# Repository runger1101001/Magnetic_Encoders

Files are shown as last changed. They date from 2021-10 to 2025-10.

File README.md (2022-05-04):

# Small encoder boards

Several designs for small magnetic encoder boards.
These boards all serve the same purpose, and many have the same shapes. They use different sensor ICs, which depending on the IC may result in different performance or different interface types.

They are intended to sense the absolute angular position of a rotating magnet. Generally this is used to sense the position of a motor shaft, as an input to motor control algorithms, or a joint/actuator position, for robotics applcations.

Where sensors use I2C, they use the Stemma-QT/Qwiic connectors (JST-SH) and pinouts.
Where sensors use SPI or SSI, they all use the same pinouts.

:warning: Not all of these have been produced or tested.

Please consult the individual subdirectories for more information. If a sub-directory does not contain a README, use at your own risk.

## Finished and tested designs

- [AS5048A](./Encoder_SPI/)
- [AS5048B](./Encoder/)
- [TLE5012B](./Encoder_SPI_TLE5012B/)
- [SC60228](./Encoder_SPI_SC60228/)

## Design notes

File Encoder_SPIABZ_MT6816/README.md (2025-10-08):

# MT6816 magnetic angle sensor

Small (21x17mm) board for the MT6816 magnetic absolute angle sensor.

For use in motor control or robotics applications, the sensor measures the orientation (angle in the plane) of a nearby diametrically magnetized magnet.

That sounds more complicated than using it really is, so lets describe it another way:

- attach the magnet to the axis of something that rotates
- put the sensor near it
- read angles with your Arduino

| Back of board | Front of board |
| --- | --- |
| with SH 1.0 connectors <br> | with sensor <br> |

## Features

- 3V to 5.5V operation
- 14 bit accuracy, 16384 positions per revolution
- SPI interface up to 15MHz
- PWM output pin with 1kHz PWM frequency and 12bit accuracy
- ABZ interface with 12 bit accuracy, 4096 steps in quadrature mode
- power indication LED (green, dim)

Datasheet of the sensor: https://www.novosns.com/enfiles/MT6816_Rev.2.1.pdf

## Getting one

You may be able to buy some here:



Or you could make one - it is open source, you will find gerber files and BOM in the repo, and design files for KiCad 6.

## Usage

The sensor has to be precisely positioned near the magnet. The magnet should be precisely on-axis and in-plane (no wobble!). The sensor should be mounted with an air-gap of about 0.5mm to the magnet.

Taking the time to mount the magnet and sensor board carefully will improve the accuracy and smoothness of your readings.

The sensor has SPI and ABZ interfaces, selectable by switch:

| SPI | ABZ |
| --- | --- |
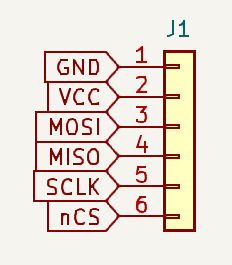
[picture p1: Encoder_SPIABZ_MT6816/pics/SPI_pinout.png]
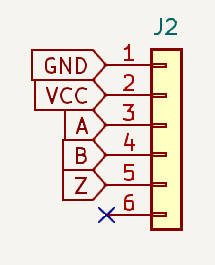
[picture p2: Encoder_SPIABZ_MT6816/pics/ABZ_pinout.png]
|  |  |

The SPI and ABZ interfaces are output on a JST-SH 6-pin socket. Pre-made cables are available cheaply on AliExpress and other sources.

You may connect VCC to either 3.3V or 5V.

For SPI, connect the other lines (MOSI, MISO, CLK and CS) to the respective counterparts on your MCU board.
Note: The sensor board does not pull the CS line up.

The ABZ and SPI outputs cannot be used at the same time. Use the switch to select the output mode.

## Communications

SPI interface:

- SPI Mode 3
- MSB first
- max 15MHz SPI clock

See [datasheet](https://www.novosns.com/enfiles/MT6816_Rev.2.1.pdf) for details, or use an existing software driver.

:warning: Note: cable length, shielding (or lack thereof) and environmental noise may limit performance to significantly less than the 10MHz maximum.

## Software

The sensor can be used with any appropriate SPI driver.

The author uses it with Arduino-compatible MCU boards and the [SimpleFOC library](http://www.simplefoc.com).

A driver for the sensor for Arduino and SimpleFOC can be found here: [SimpleFOC drivers library](https://github.com/simplefoc/Arduino-FOC-drivers/tree/master/src/encoders/mt6816)

## Physical dimensions

v1.0: 21 x 17 x 4mm (1.6mm PCB)

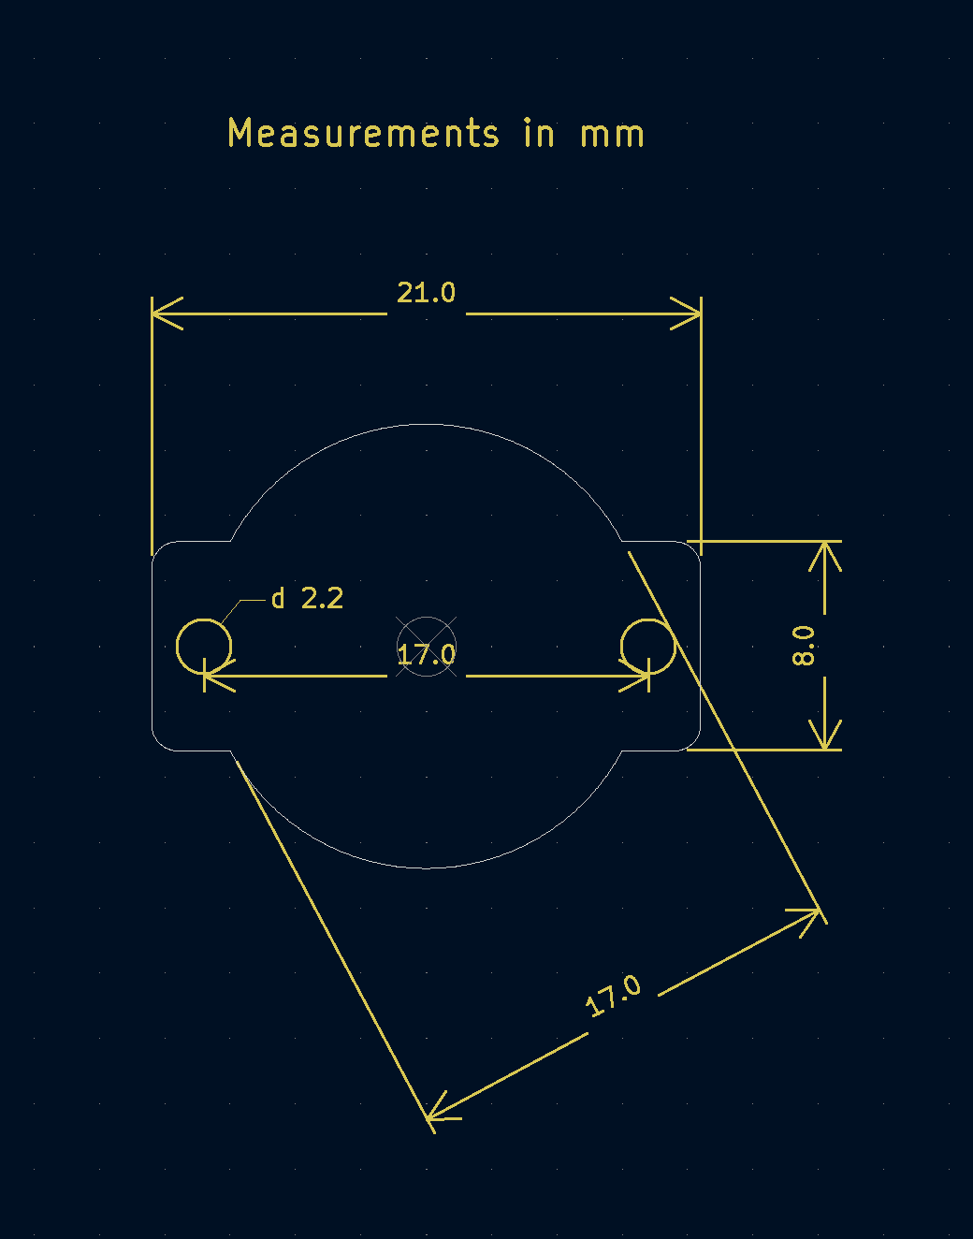
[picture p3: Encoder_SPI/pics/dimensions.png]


## Cables

Pre-made JST SH 1.0 cables are available. When buying cables with two plugs, choose the type that is called "reverse connection" - where the pins on both ends of the cable have the same order.

Some links to compatible cables / breakout boards:

- https://www.tindie.com/products/26431/
- https://www.aliexpress.com/item/4000421829259.html
- https://www.aliexpress.com/item/4001235017139.html
- https://www.pololu.com/product/4770
- https://www.pololu.com/product/4772

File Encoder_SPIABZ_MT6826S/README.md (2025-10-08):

# MT6826S magnetic angle sensor

Small (21x17mm) board for the MT6826S magnetic absolute angle sensor.

For use in motor control or robotics applications, the sensor measures the orientation (angle in the plane) of a nearby diametrically magnetized magnet.

That sounds more complicated than using it really is, so lets describe it another way:
- attach the magnet to the axis of something that rotates
- put the sensor near it
- read angles with your Arduino

| Back of board | Front of board |
| --- | --- |
| with SH 1.0 connectors <br> | with sensor <br> |

## Features

- 3V to 5V operation
- 15 bit accuracy, 32768 positions per revolution 
- SPI interface up to 15Hz
- PWM output pin with 1kHz PWM frequency and 12bit accuracy
- ABZ interface with 14 bit accuracy, 16384 steps in quadrature mode
- power indication LED (green, dim)

Datasheet of the sensor: https://www.novosns.com/enfiles/MT6826S_Datasheet_Rev.1.1.pdf

## Getting one

You may be able to buy some here:



Or you could make one - it is open source, you will find gerber files and BOM in the repo, and design files for KiCad 6.

## Usage

The sensor has to be precisely positioned near the magnet. The magnet should be precisely on-axis and in-plane (no wobble!). The sensor should be mounted with an air-gap of about 0.5mm to the magnet.

Taking the time to mount the magnet and sensor board carefully will improve the accuracy and smoothness of your readings.

The sensor has SPI and ABZ interfaces:

|SPI|ABZ|
|---|---|
|||

The SPI interface is available on a JST-SH 6-pin socket. Pre-made cables are available cheaply on AliExpress and other sources.

You may connect VCC to either 3.3V or 5V, but must set the solder jumper accordingly. The default setting of the solder jumper is 3.3V. To use 5V power, carefully cut the trace connecting the two pads of the jumper. 

For SPI, connect the other lines (MOSI, MISO, CLK and CS) to the respective counterparts on your MCU board.

The ABZ outputs can be used in parallel to the SPI interface.

Note: The sensor board does not pull the CS line up.

## Communications

SPI interface:
- SPI Mode 3
- MSB first
- max 15MHz SPI clock

See [datasheet](https://www.novosns.com/enfiles/MT6826S_Datasheet_Rev.1.1.pdf) for details, or use an existing software driver.

:warning: Note: cable length, shielding (or lack thereof) and environmental noise may limit performance to significantly less than the 10MHz maximum.

## Software

The sensor can be used with any appropriate SPI driver.

The author uses it with Arduino-compatible MCU boards and the [SimpleFOC library](http://www.simplefoc.com).

A driver for the sensor for Arduino and SimpleFOC can be found here: [SimpleFOC drivers library](https://github.com/simplefoc/Arduino-FOC-drivers/tree/master/src/encoders/mt6826s)

## Physical dimensions

v1.0: 21 x 17 x 4mm (1.6mm PCB)



## Cables

Pre-made JST SH 1.0 cables are available. When buying cables with two plugs, choose the type that is called "reverse connection" - where the pins on both ends of the cable have the same order.

Some links to compatible cables / breakout boards:

 - https://www.tindie.com/products/26431/
 - https://www.aliexpress.com/item/4000421829259.html
 - https://www.aliexpress.com/item/4001235017139.html
 - https://www.pololu.com/product/4770
 - https://www.pololu.com/product/4772

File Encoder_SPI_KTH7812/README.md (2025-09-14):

# KTH7812 magnetic angle sensor

Small (21x17mm) board for the KTH7812 magnetic absolute angle sensor with high resolution.

For use in motor control or robotics applications, the sensor measures the orientation (angle in the plane) of a nearby diametrically magnetized magnet.

That sounds more complicated than using it really is, so lets describe it another way:
- attach the magnet to the axis of something that rotates
- put the sensor near it
- read angles with your Arduino

| Back of board | Front of board |
| --- | --- |
| with SH 1.0 connector  | with sensor  |

## Features

- 3.3V to 5V operation
- 16 bit resolution, 65536 positions per revolution
- SPI interface up to 10MHz
- power indication LED (green, dim)

Datasheet of the sensor: [KTH7812_产品手册.pdf](https://en.conntek.com.cn/html/web/product/magneticAngleDetectionChip/hshrMagneticCodedAngleSensor/index.html
https://en.conntek.com.cn/api/resource/freeDownload?name=KTH7812%20产品手册.pdf)

## Getting one

You may be able to buy some here:



Or you could make one - it is open source, you will find gerber files and BOM in the repo, and design files for KiCad 9.

## Usage

The sensor has to be precisely positioned near the magnet. The magnet should be precisely on-axis and in-plane (no wobble!). The sensor should be mounted with an air-gap of about 0.5mm to the magnet.

Taking the time to mount the magnet and sensor board carefully will improve the accuracy and smoothness of your readings.

The sensor has an SPI interface:

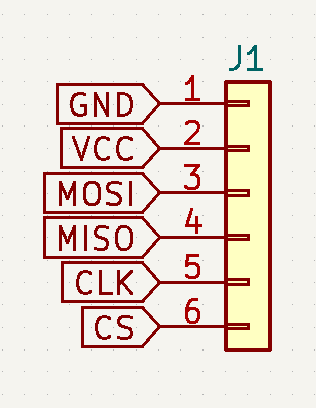
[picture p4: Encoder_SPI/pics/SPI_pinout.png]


The SPI interface is available on a JST-SH 6-pin socket. Pre-made cables are available cheaply on AliExpress and other sources.

You may connect VCC to either 3.3V or 5V. 

Connect the other lines (MOSI, MISO, CLK and CS) to the respective counterparts on your MCU board.

Note: The sensor board does not pull the CS line up.

## Communications

SPI interface:
- SPI Mode 3
- MSB first
- max 10MHz SPI clock

See [datasheet](https://en.conntek.com.cn/html/web/product/magneticAngleDetectionChip/hshrMagneticCodedAngleSensor/index.html
https://en.conntek.com.cn/api/resource/freeDownload?name=KTH7812%20产品手册.pdf) for details, or use an existing software driver.

:warning: Note: cable length, shielding (or lack thereof) and environmental noise may limit performance to significantly less than the 10MHz maximum.

## Software

The sensor can be used with any appropriate SPI driver.

The author uses it with Arduino-compatible MCU boards and the [SimpleFOC library](http://www.simplefoc.com).

A driver for the sensor for Arduino and SimpleFOC can be found here: [SimpleFOC drivers library](https://github.com/simplefoc/Arduino-FOC-drivers/tree/master/src/encoders/KTH7812)

## Physical dimensions

v1.0: 21 x 17 x 4mm (1.6mm PCB)



## Cables

Pre-made JST SH 1.0 cables are available. When buying cables with two plugs, choose the type that is called "reverse connection" - where the pins on both ends of the cable have the same order.

Some links to compatible cables / breakout boards:

 - https://www.tindie.com/products/26431/
 - https://www.aliexpress.com/item/4000421829259.html
 - https://www.aliexpress.com/item/4001235017139.html
 - https://www.pololu.com/product/4770
 - https://www.pololu.com/product/4772

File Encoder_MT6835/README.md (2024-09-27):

# MT6835 magnetic angle sensor

Small (21x17mm) board for the MT6835 magnetic absolute angle sensor.

For use in motor control or robotics applications, the sensor measures the orientation (angle in the plane) of a nearby diametrically magnetized magnet.

That sounds more complicated than using it really is, so lets describe it another way:
- attach the magnet to the axis of something that rotates
- put the sensor near it
- read angles with your Arduino

| Back of board | Front of board |
| --- | --- |
| with SH 1.0 connectors <br> | with sensor <br> |

## Features

- 3V to 5V operation
- 21 bit accuracy, 2097152 positions per revolution (!)
- ABZ interface with 16 bit accuracy, 65536 steps in quadrature mode (!)
- SPI interface up to 15MHz
- PWM output pin with 994Hz PWM frequency and 12bit accuracy
- On-chip linearity calibration
- power indication LED (green, dim)

Datasheet of the sensor: https://www.magntek.com.cn/upload/MT6835_Rev.1.3.pdf

## Getting one

You may be able to buy some here:



Or you could make one - it is open source, you will find gerber files and BOM in the repo, and design files for KiCad 6.

## Usage

The sensor has to be precisely positioned near the magnet. The magnet should be precisely on-axis and in-plane (no wobble!). The sensor should be mounted with an air-gap of about 0.5mm to the magnet.

Taking the time to mount the magnet and sensor board carefully will improve the accuracy and smoothness of your readings.

The sensor has SPI and ABZ interfaces:

|SPI|ABZ|
|---|---|
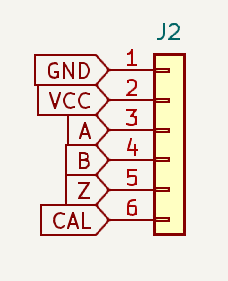
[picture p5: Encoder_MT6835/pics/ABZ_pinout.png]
|||

The SPI interface is available on a JST-SH 6-pin socket. Pre-made cables are available cheaply on AliExpress and other sources.

You may connect VCC to either 3.3V or 5V.

For SPI, connect the other lines (MOSI, MISO, CLK and CS) to the respective counterparts on your MCU board.

The ABZ outputs can be used in parallel to the SPI interface.

The CAL pin on the ABZ interface gives feedback on the built-in calibration procedure (see datasheet). It can be ignored if not needed.

Note: the sensor chip's ABZ interface is disabled by default. You have to enable it and set the resolution using the SPI interface.

Note: The sensor board does not pull the CS line up.

## Communications

SPI interface:
- SPI Mode 3
- MSB first
- max 15MHz SPI clock

See [datasheet](https://www.magntek.com.cn/upload/MT6835_Rev.1.3.pdf) for details, or use an existing software driver.

:warning: Note: cable length, shielding (or lack thereof) and environmental noise may limit performance to significantly less than the 15MHz maximum.

## Software

The sensor can be used with any appropriate SPI driver.

The author uses it with Arduino-compatible MCU boards and the [SimpleFOC library](http://www.simplefoc.com).

A driver for the sensor for Arduino and SimpleFOC can be found here: [SimpleFOC drivers library](https://github.com/simplefoc/Arduino-FOC-drivers/tree/master/src/encoders/mt6835)

## Physical dimensions

v1.0: 21 x 17 x 4mm (1.6mm PCB)



3D model: [STEP file](./Encoder_MT6835.step)

## Cables

Pre-made JST SH 1.0 cables are available. When buying cables with two plugs, choose the type that is called "reverse connection" - where the pins on both ends of the cable have the same order.

Some links to compatible cables / breakout boards:

 - https://www.tindie.com/products/26431/
 - https://www.aliexpress.com/item/4000421829259.html
 - https://www.aliexpress.com/item/4001235017139.html
 - https://www.pololu.com/product/4770
 - https://www.pololu.com/product/4772

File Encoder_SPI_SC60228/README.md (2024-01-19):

# SC60228 magnetic angle sensor

Small (21x17mm) board for the SC60228 magnetic absolute angle sensor.

For use in motor control or robotics applications, the sensor measures the orientation (angle in the plane) of a nearby diametrically magnetized magnet.

That sounds more complicated than using it really is, so lets describe it another way:
- attach the magnet to the axis of something that rotates
- put the sensor near it
- read angles with your Arduino

| Back of board | Front of board |
| --- | --- |
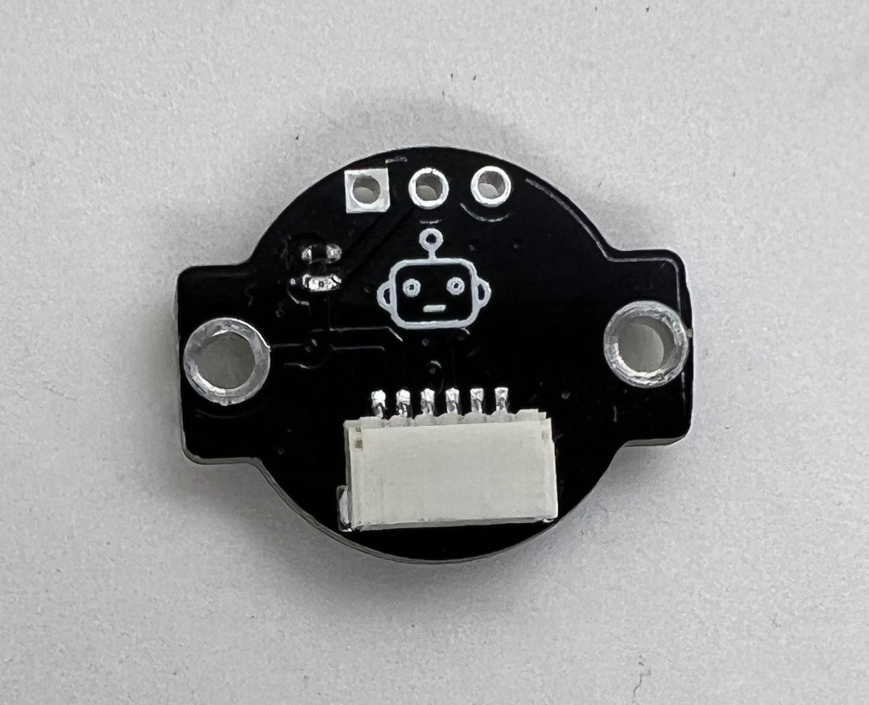
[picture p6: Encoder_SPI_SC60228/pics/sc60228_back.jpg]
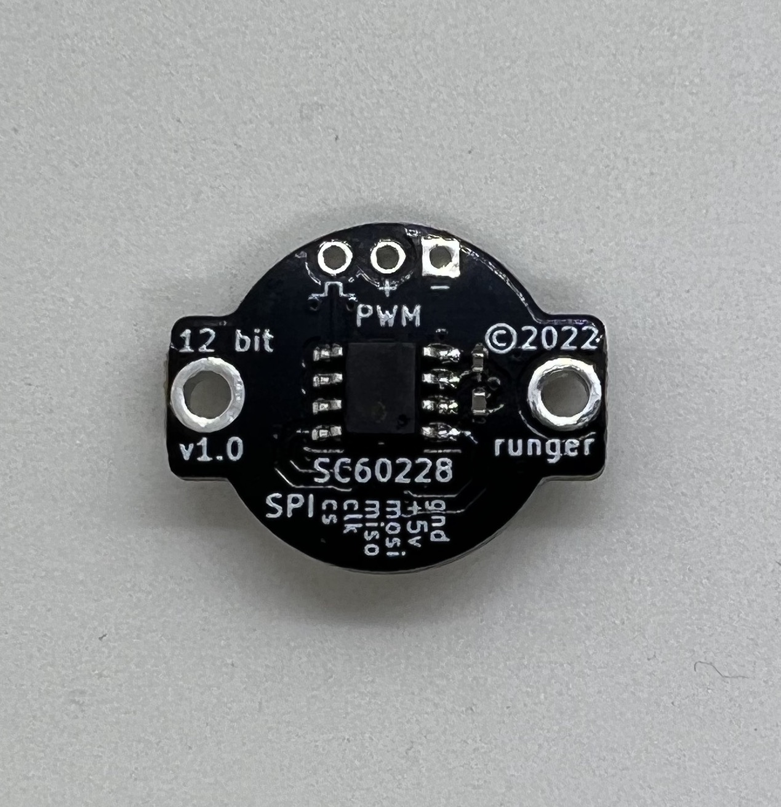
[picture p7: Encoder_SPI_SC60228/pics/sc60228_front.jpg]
| with SH 1.0 connector  | with sensor  |

## Features

- 3V to 5V operation
- 12 bit accuracy, 4096 positions per revolution 
- SPI interface up to 10MHz
- power indication LED (green, dim)

Datasheet of the sensor: http://www.semiment.com/download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

## Getting one

You may be able to buy some here:



Or you could make one - it is open source, you will find gerber files and BOM in the repo, and design files for KiCad 6.

## Usage

The sensor has to be precisely positioned near the magnet. The magnet should be precisely on-axis and in-plane (no wobble!). The sensor should be mounted with an air-gap of about 0.5mm to the magnet.

Taking the time to mount the magnet and sensor board carefully will improve the accuracy and smoothness of your readings.

The sensor has an SPI interface:



The SPI interface is available on a JST-SH 6-pin socket. Pre-made cables are available cheaply on AliExpress and other sources.

You may connect VCC to either 3.3V or 5V. 

Connect the other lines (MOSI, MISO, CLK and CS) to the respective counterparts on your MCU board.

Note: The sensor board does not pull the CS line up.

## Communications

SPI interface:
- SPI Mode 1
- MSB first
- max 10MHz SPI clock

See [datasheet](http://www.semiment.com/download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) for details, or use an existing software driver.

:warning: Note: cable length, shielding (or lack thereof) and environmental noise may limit performance to significantly less than the 10MHz maximum.

## Software

The sensor can be used with any appropriate SPI driver.

The author uses it with Arduino-compatible MCU boards and the [SimpleFOC library](http://www.simplefoc.com).

A driver for the sensor for Arduino and SimpleFOC can be found here: [SimpleFOC drivers library](https://github.com/simplefoc/Arduino-FOC-drivers/tree/master/src/encoders/sc60228)

## Physical dimensions

v1.0: 21 x 17 x 4mm (1.6mm PCB)



## Cables

Pre-made JST SH 1.0 cables are available. When buying cables with two plugs, choose the type that is called "reverse connection" - where the pins on both ends of the cable have the same order.

Some links to compatible cables / breakout boards:

 - https://www.tindie.com/products/26431/
 - https://www.aliexpress.com/item/4000421829259.html
 - https://www.aliexpress.com/item/4001235017139.html
 - https://www.pololu.com/product/4770
 - https://www.pololu.com/product/4772

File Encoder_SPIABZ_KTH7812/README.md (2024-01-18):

# AS5047P magnetic angle sensor

Small (21x17mm) board for the AS5047P magnetic absolute angle sensor.

For use in motor control or robotics applications, the sensor measures the orientation (angle in the plane) of a nearby diametrically magnetized magnet.

That sounds more complicated than using it really is, so lets describe it another way:
- attach the magnet to the axis of something that rotates
- put the sensor near it
- read angles with your Arduino

| Back of board | Front of board |
| --- | --- |
| with SH 1.0 connectors <br> | with sensor <br> |

## Features

- 3V to 5V operation
- 14 bit accuracy, 16384 positions per revolution 
- SPI interface up to 10MHz
- PWM output pin with 1kHz PWM frequency and 12bit accuracy
- ABZ interface with 12 bit accuracy, 4096 steps in quadrature mode
- power indication LED (green, dim)

Datasheet of the sensor: https://ams.com/documents/20143/36005/AS5047P_DS000324_3-00.pdf

## Getting one

You may be able to buy some here:



Or you could make one - it is open source, you will find gerber files and BOM in the repo, and design files for KiCad 6.

## Usage

The sensor has to be precisely positioned near the magnet. The magnet should be precisely on-axis and in-plane (no wobble!). The sensor should be mounted with an air-gap of about 0.5mm to the magnet.

Taking the time to mount the magnet and sensor board carefully will improve the accuracy and smoothness of your readings.

The sensor has SPI and ABZ interfaces:

|SPI|ABZ|
|---|---|
|||

The SPI interface is available on a JST-SH 6-pin socket. Pre-made cables are available cheaply on AliExpress and other sources.

You may connect VCC to either 3.3V or 5V, but must set the solder jumper accordingly. The default setting of the solder jumper is 3.3V. To use 5V power, carefully cut the trace connecting the two pads of the jumper. 

For SPI, connect the other lines (MOSI, MISO, CLK and CS) to the respective counterparts on your MCU board.

The ABZ outputs can be used in parallel to the SPI interface.

Note: The sensor board does not pull the CS line up.

## Communications

SPI interface:
- SPI Mode 1
- MSB first
- max 10MHz SPI clock

See [datasheet](https://ams.com/documents/20143/36005/AS5047P_DS000324_3-00.pdf) for details, or use an existing software driver.

:warning: Note: cable length, shielding (or lack thereof) and environmental noise may limit performance to significantly less than the 10MHz maximum.

## Software

The sensor can be used with any appropriate SPI driver.

The author uses it with Arduino-compatible MCU boards and the [SimpleFOC library](http://www.simplefoc.com).

A driver for the sensor for Arduino and SimpleFOC can be found here: [SimpleFOC drivers library](https://github.com/simplefoc/Arduino-FOC-drivers/tree/master/src/encoders/as5047)

## Physical dimensions

v1.0: 21 x 17 x 4mm (1.6mm PCB)



3D model: [STEP file](./Encoder_SPI_AS5047P.step)

## Cables

Pre-made JST SH 1.0 cables are available. When buying cables with two plugs, choose the type that is called "reverse connection" - where the pins on both ends of the cable have the same order.

Some links to compatible cables / breakout boards:

 - https://www.tindie.com/products/26431/
 - https://www.aliexpress.com/item/4000421829259.html
 - https://www.aliexpress.com/item/4001235017139.html
 - https://www.pololu.com/product/4770
 - https://www.pololu.com/product/4772

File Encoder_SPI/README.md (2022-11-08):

# AS5048A magnetic angle sensor

Small (21x17mm) board for the AS5048A magnetic absolute angle sensor.

For use in motor control or robotics applications, the sensor precisely measures the orientation (angle in the plane) of a nearby diametrically magnetized magnet.

That sounds more complicated than using it really is, so lets describe it another way:
- attach the magnet to the axis of something that rotates
- put the sensor near it
- read precise angles with your Arduino

| Back of board | Front of board |
| --- | --- |
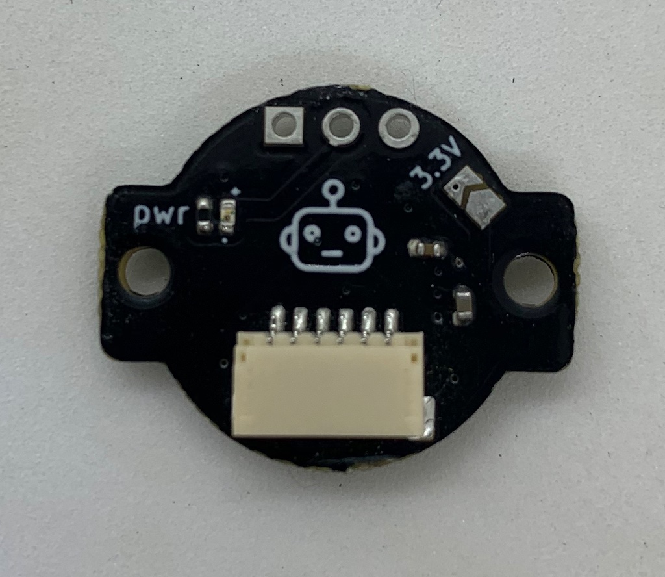
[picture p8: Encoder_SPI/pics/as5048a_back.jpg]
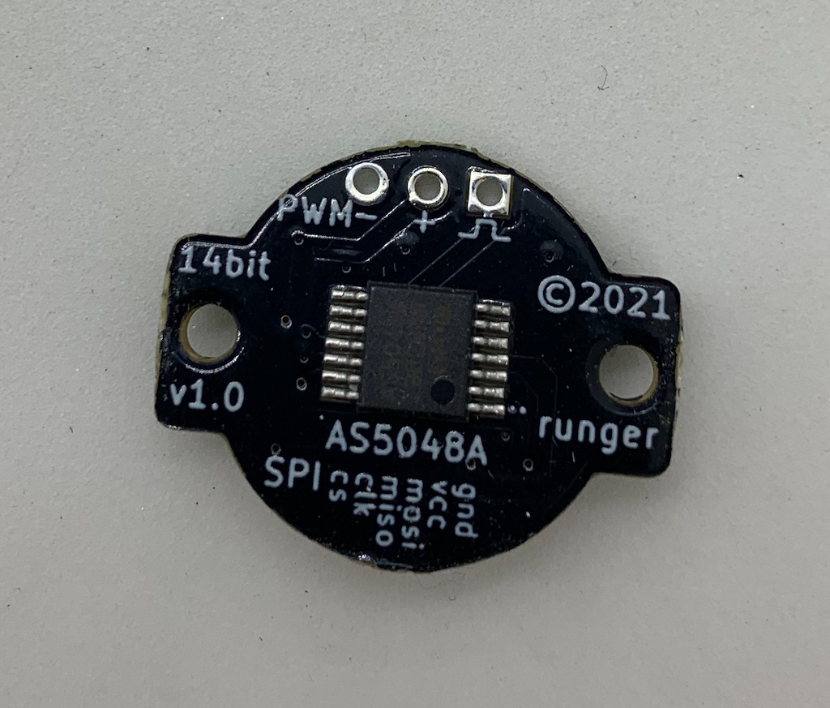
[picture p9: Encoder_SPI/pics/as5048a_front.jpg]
| with SH 1.0 connector  | with sensor  |

## Features

- 3.3V (default) or 5V (break solder bridge for 5V)
- 14 bit accuracy, 16384 positions per revolution 
- SPI interface up to 10MHz
- PWM output pin with 1kHz PWM frequency and 12bit accuracy
- power indication LED (green, dim)

Datasheet of the sensor: https://ams.com/documents/20143/36005/AS5048_DS000298_4-00.pdf

## Getting one

You may be able to buy some here:



Or you could make one - it is open source, you will find gerber files and BOM in the repo, and design files for KiCad 6.

## Getting help

Please visit our discord: https://discord.gg/FwTymtVhMU

Or if you have found a problem, you can also open a bug-ticket here on GitHub.

## Usage

The sensor has to be precisely positioned near the magnet. The magnet should be precisely on-axis and in-plane (no wobble!). The sensor should be mounted with an air-gap of about 0.5mm to the magnet.

Taking the time to mount the magnet and sensor board carefully will improve the accuracy and smoothness of your readings.

The sensor has an SPI interface:



The SPI interface is available on a JST-SH 6-pin socket. Pre-made cables are available cheaply on AliExpress and other sources.

You may connect VCC to either 3.3V or 5V. 

Sensor board v1.1 (current version):

- If using 5V, break the connection between the solder bridge pads on the back side of the board.
- If using 3.3V, leave as is, do not break the solder-bridge.

Sensor board v1.0 (older version):

- If using 5V, leave the connection between the solder bridge pads on the back side of the board open.
- If using 3.3V, close the solder-bridge.

| 5V | 3.3V |
| :---: | :---: |
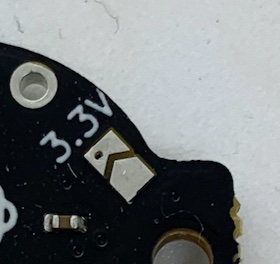
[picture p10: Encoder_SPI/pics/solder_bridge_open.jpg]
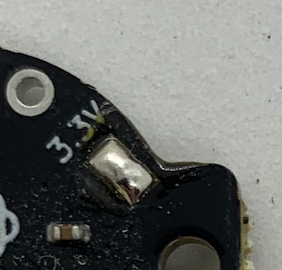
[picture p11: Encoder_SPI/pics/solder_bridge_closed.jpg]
|    |  |

Connect the other lines (MOSI, MISO, CLK and CS) to the respective counterparts on your MCU board.

Note: The sensor board does not pull the CS line up.

## Communications

SPI interface:
- SPI Mode 1
- MSB first
- max 10MHz SPI clock

See [datasheet](https://ams.com/documents/20143/36005/AS5048_DS000298_4-00.pdf) for details, or use an existing software driver.

:warning: Note: cable length, shielding (or lack thereof) and environmental noise may limit performance to significantly less than the 10MHz maximum.

## Software

The sensor can be used with any appropriate SPI driver.

The author uses it with Arduino-compatible MCU boards and the [SimpleFOC library](http://www.simplefoc.com).

A driver for the sensor for Arduino and SimpleFOC can be found here: [SimpleFOC drivers library](https://github.com/simplefoc/Arduino-FOC-drivers/tree/master/src/encoders/as5048a)

## Physical dimensions

v1.1: 21 x 17 x 3.4mm (1mm PCB)
v1.0: 21 x 17 x 4mm (1.6mm PCB)



## Cables

Pre-made JST SH 1.0 cables are available. When buying cables with two plugs, choose the type that is called "reverse connection" - where the pins on both ends of the cable have the same order.

Some links to compatible cables / breakout boards:

 - https://www.tindie.com/products/26431/
 - https://www.aliexpress.com/item/4000421829259.html
 - https://www.aliexpress.com/item/4001235017139.html
 - https://www.pololu.com/product/4770
 - https://www.pololu.com/product/4772

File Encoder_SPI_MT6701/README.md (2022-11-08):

# MT6701 magnetic angle sensor

Small (21x17mm) board for the MT6701 magnetic absolute angle sensor.

For use in motor control or robotics applications, the sensor precisely measures the orientation (angle in the plane) of a nearby diametrically magnetized magnet.

That sounds more complicated than using it really is, so lets describe it another way:
- attach the magnet to the axis of something that rotates
- put the sensor near it
- read precise angles with your Arduino

| Back of board | Front of board |
| --- | --- |
| with SH 1.0 connector  | with sensor  |

## Features

- 3.3V or 5V power
- SSI, ABZ and I2C digital interfaces (SH 1.0 connector)
- Analog interface (solder pad)
- Push interface (solder pad)
- 14 bit accuracy, 16384 positions per revolution on SSI and I2C
- 12 bit accuracy, 4096 positions per revolution on ABZ and analog
- SSI interface up to 10MHz
- power indication LED (green, dim)
- seperate I2C programming board available, see [here]().

Datasheet of the sensor: 

## Getting one

You may be able to buy some here:



Or you could make one - it is open source, you will find gerber files and BOM in the repo, and design files for KiCad 6.

## Getting help

Please visit our discord: https://discord.gg/FwTymtVhMU

Or if you have found a problem, you can also open a bug-ticket here on GitHub.

## Usage

The sensor has to be precisely positioned near the magnet. The magnet should be precisely on-axis and in-plane (no wobble!). The sensor should be mounted with an air-gap of about 0.5mm to the magnet.

Taking the time to mount the magnet and sensor board carefully will improve the accuracy and smoothness of your readings.

The sensor's SSI / ABZ / I2C interface has the following pin-out:

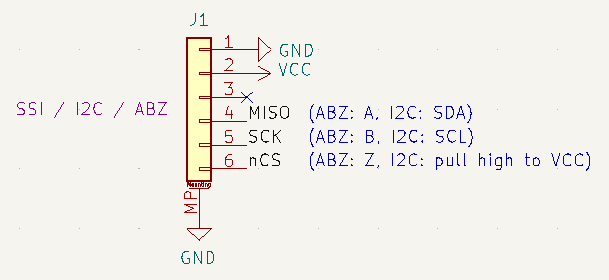
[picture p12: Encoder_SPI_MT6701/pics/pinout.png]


The SSI / ABZ / I2C interface is available on the JST-SH 6-pin socket. Pre-made cables are available cheaply on AliExpress and other sources.

You can switch between ABZ mode and SSI / I2C mode using the small switch on the back of the sensor board. Don't change the mode while the sensor is powered. When in ABZ mode, the sensor will output encoder pulses (see pinout).
When in SSI / ABZ mode, connect the nCS 

You may connect VCC to either 3.3V or 5V. 

Connect the other lines to the respective counterparts on your MCU board according the pinout shown above.

Note: The sensor board does not pull the CS line up.

## Communications

SPI interface:
- SPI Mode 1
- MSB first
- max 10MHz SPI clock

See [datasheet]() for details, or use an existing software driver.

:warning: Note: cable length, shielding (or lack thereof) and environmental noise may limit performance to significantly less than the 10MHz maximum.

## Software

The sensor can be used with any appropriate SPI driver.

The author uses it with Arduino-compatible MCU boards and the [SimpleFOC library](http://www.simplefoc.com).

A driver for the sensor for Arduino and SimpleFOC can be found here: [SimpleFOC drivers library](https://github.com/simplefoc/Arduino-FOC-drivers/tree/master/src/encoders/mt6701)

## Physical dimensions

21 x 17 x 4mm (1.6mm PCB)



## Cables

Pre-made JST SH 1.0 cables are available. When buying cables with two plugs, choose the type that is called "reverse connection" - where the pins on both ends of the cable have the same order.

Some links to compatible cables / breakout boards:

 - https://www.tindie.com/products/26431/
 - https://www.aliexpress.com/item/4000421829259.html
 - https://www.aliexpress.com/item/4001235017139.html
 - https://www.pololu.com/product/4770
 - https://www.pololu.com/product/4772

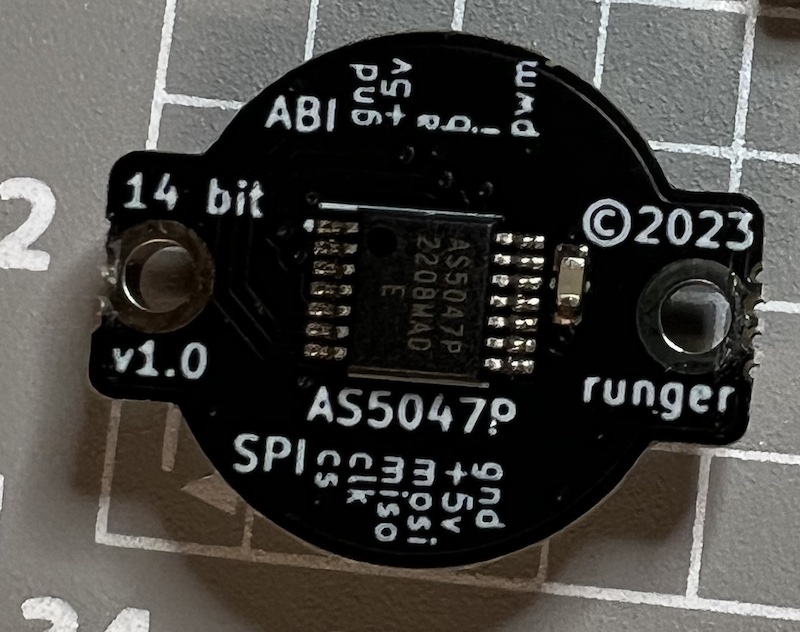
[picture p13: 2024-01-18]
Encoder_SPI_AS5047P_big/pics/as5047p_front.jpg

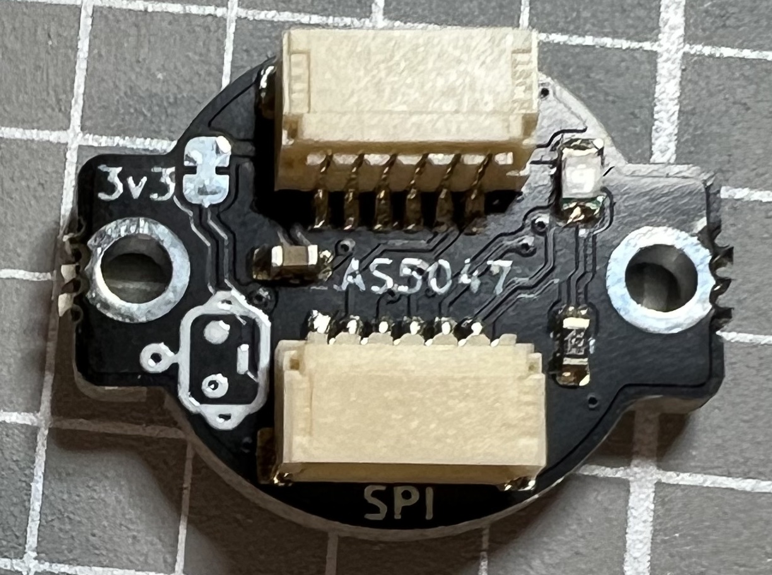
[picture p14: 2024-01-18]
Encoder_SPI_AS5047P_big/pics/as5047p_back.jpg

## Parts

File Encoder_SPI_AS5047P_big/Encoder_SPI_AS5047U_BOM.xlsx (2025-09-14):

Item | Ref Des | Qty | Manufacturer | Mfg Part # | Description / Value | Package | Type | Your Instructions / Notes
1 | C1 | 1 | Generic | 1uF 10V | 1uF 10V | C_0603_1608Metric | SMD | eg. YAGEO CC0603KRX7R6BB105; Unpolarized capacitor;
2 | C2 | 1 | Generic | 100nF 10V | 100nF 10V | C_0603_1608Metric | SMD | eg. YAGEO CC0603KRX7R6BB104; Unpolarized capacitor;
3 | D1 | 1 | Generic | Green LED | green | LED_0805_2012Metric | SMD | e.g. XINGLIGHT XL-2012UGC; Light emitting diode;
4 | J1,J2 | 2 | Scondar Electronic Limited | SCT-WR-S-06P | Conn_01x06_MountingPin | JST_SH_SM06B-SRSS-TB_1x06-1MP_P1.00mm_Horizontal | SMD | compatible to JST SH_SM06B-SRSS-TB_1x06-1MP_P1.00mm_Horizontal; Generic connectable mounting pin connector, single row, 01x06, script generated (kicad-library-utils/schlib/autogen/connector/);
5 | R1 | 1 | Generic | Generic 4k7 Resistor | 4k7 | R_0603_1608Metric | SMD | ; Resistor;
6 | U2 | 1 | AMS | AS5047U-HTSM | AS5047P or AS5047U | TSSOP-14_4.4x5mm_P0.65mm | SMD | or AS5047P-ATSM, depends on price

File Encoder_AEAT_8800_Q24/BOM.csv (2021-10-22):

Item | Ref Des | Qty | Manufacturer | Mfg Part # | Description / Value | Package | Type | Your Instructions / Notes
1 | C1 | 1 | AVX | 04026D104KAT2A | 100nF 6.3V | C_0402_1005Metric | ? | or similar 6.3V 100nF capacitor; Unpolarized capacitor;
2 | C2 | 1 | Murata | GRM155R60J106ME15D | 10uF 6.3V | C_0402_1005Metric | ? | or other 6.3V 10uF capacitor; Unpolarized capacitor;
3 | D1 | 1 | Wurth | 150040VS73240 | green | LED_0402_1005Metric | ? | ; Light emitting diode;
4 | H2,H1 | 2 |  | Mounting Hole with connection | MountingHole_Pad | MountingHole_Pad_1.75mm_2.75mm | ? | ; Mounting Hole with connection;
5 | J1 | 1 | JST | SH_SM06B-SRSS-TB_1x06-1MP_P1.00mm_Horizontal | Conn_01x06_MountingPin | JST_SH_SM06B-SRSS-TB_1x06-1MP_P1.00mm_Horizontal | ? | ; Generic connectable mounting pin connector, single row, 01x06, script generated (kicad-library-utils/schlib/autogen/connector/);
6 | J2 | 1 |  | Generic connector, single row, 01x06, script generated (kicad-library-utils/schlib/autogen/connector/) | Castellations_SPI | Castellations_x6_1.5p_1hole | ? | ; Generic connector, single row, 01x06, script generated (kicad-library-utils/schlib/autogen/connector/);
7 | R1 | 1 | Generic | Generic | 1k | R_0402_1005Metric | ? | ; Resistor;
8 | U1 | 1 | Broadcom | AEAT-8800-Q24TR | AEAT_8800_Q24 | QFN-24-1EP_5x5mm_P0.65mm_EP3.2x3.2mm | ? | ; 10- to 16-Bit Programmable Angular Magnetic Encoder; https://docs.broadcom.com/doc/pub-005892

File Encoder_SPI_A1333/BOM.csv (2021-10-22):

Item | Ref Des | Qty | Manufacturer | Mfg Part # | Description / Value | Package | Type | Your Instructions / Notes
1 | C1,C2 | 2 | Generic | Generic | 100nF 6.3V | C_0402_1005Metric | ? | ; Unpolarized capacitor;
2 | D1 | 1 | Wurth | 150040VS73240 | green | LED_0402_1005Metric | ? | ; Light emitting diode;
3 | H2,H1 | 2 |  | Mounting Hole with connection | MountingHole_Pad | MountingHole_2.2mm_M2_ISO7380_Pad | ? | ; Mounting Hole with connection;
4 | J1 | 1 | JST | SH_SM06B-SRSS-TB_1x06-1MP_P1.00mm_Horizontal | Conn_01x06_MountingPin | JST_SH_SM06B-SRSS-TB_1x06-1MP_P1.00mm_Horizontal | ? | ; Generic connectable mounting pin connector, single row, 01x06, script generated (kicad-library-utils/schlib/autogen/connector/);
5 | J2 | 1 |  | Generic connector, single row, 01x04, script generated (kicad-library-utils/schlib/autogen/connector/) | Castellations_ABI | PinHeader_1x04_P2.54mm_Vertical | ? | ; Generic connector, single row, 01x04, script generated (kicad-library-utils/schlib/autogen/connector/);
6 | R1 | 1 | Generic | Generic 1k Resistor | 1k | R_0402_1005Metric | ? | ; Resistor;
7 | U1 | 1 | Allegro | A1333LLETR-T | A1333 | TSSOP-14_4.4x5mm_P0.65mm | ? | ; Precision, High Speed, Hall-Effect Angle Sensor IC with Integrated Diagnostics for Safety-Critical Applications, 3.3V;

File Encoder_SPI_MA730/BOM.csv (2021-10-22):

Item | Ref Des | Qty | Manufacturer | Mfg Part # | Description / Value | Package | Type | Your Instructions / Notes
1 | C2 | 1 | Generic | Generic | 1uF 6.3V | C_0402_1005Metric | ? | ; Unpolarized capacitor;
2 | D1 | 1 | Wurth | 150040VS73240 | green | LED_0402_1005Metric | ? | ; Light emitting diode;
3 | H2,H1 | 2 |  | Mounting Hole with connection | MountingHole_Pad | MountingHole_2.2mm_M2_ISO7380_Pad | ? | ; Mounting Hole with connection;
4 | J1 | 1 | JST | SH_SM08B-SRSS-TB_1x08-1MP_P1.00mm_Horizontal | Conn_01x06_MountingPin | JST_SH_SM08B-SRSS-TB_1x08-1MP_P1.00mm_Horizontal | ? | ; Generic connectable mounting pin connector, single row, 01x08, script generated (kicad-library-utils/schlib/autogen/connector/);
5 | J2 | 1 |  | Generic connector, single row, 01x04, script generated (kicad-library-utils/schlib/autogen/connector/) | Castellations_ABI | PinHeader_1x04_P2.54mm_Vertical | ? | ; Generic connector, single row, 01x04, script generated (kicad-library-utils/schlib/autogen/connector/);
6 | R1 | 1 |  | Resistor | 1k | R_0402_1005Metric | ? | ; Resistor;
7 | U1 | 1 |  | Magnetic rotary angle sensor, 14-bit, SPI interface, ABZ, PWM, QFN-16 | MA730 | QFN-16-1EP_3x3mm_P0.5mm_EP1.75x1.75mm | ? | ; Magnetic rotary angle sensor, 14-bit, SPI interface, ABZ, PWM, QFN-16; https://www.monolithicpower.com/pub/media/document/m/a/ma730_r1.01.pdf

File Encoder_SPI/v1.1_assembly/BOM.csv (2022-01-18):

Item # | Ref Des | Qty | Manufacturer | Mfg Part # | Description / Value | Package | Type | Your Instructions / Notes
1 | U1 | 1 | AMS | AS5048A | AS5048A | TSSOP-14_4.4x5mm_P0.65mm | SMD
2 | J1 | 1 | JST | JST_SH_SM06B-SRSS-TB_1x06-1MP | JST SH 1.0mm 6-pin horizontal socket | JST_SH_SM06B-SRSS-TB_1x06-1MP_P1.00mm_Horizontal | SMD
7 | R5 | 1 | Generic | Generic | 4k7 | R_0402_1005Metric | SMD
8 | D1 | 1 | ROHM | SML-P12MTT86 | Green LED | LED_0402_1005Metric | SMD | Please choose inexpensive green LED, for example ROHM SML-P13FTT86R
9 | C2 | 1 | Samsung | CL05B104KQ5NNNC | 100nF 6.3V Ceramic | C_0402_1005Metric | SMD
10 | C1 | 1 | Murata | ZRB15XR61A106ME01D | 10uF 10V Ceramic | C_0402_1005Metric | SMD

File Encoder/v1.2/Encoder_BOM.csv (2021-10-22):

Item # | Ref Des | Qty | Manufacturer | Mfg Part # | Description / Value | Package | Type | Your Instructions / Notes
1 | C1 | 1 | Generic | Generic | 10µF 6.3V Ceramic | 0402 | SMD | Generic
2 | C2 | 1 | Generic | Generic | 100nF 6.3V Ceramic | 0402 | SMD | Generic
3 | D1 | 1 | Generic | e.g.: SML-P13PT | LED Green (λ 560nm) Vf 2.1V @20mA | 0402 | SMD | Generic, e.g. https://eu.mouser.com/datasheet/2/348/sml-p1-e-1874493.pdf
4 | J1 | 1 | JST | SM04B-SRSS-TB | Conn_01x04 | SM04B-SRSS-TB | SMD | http://www.jst-mfg.com/product/pdf/eng/eSH.pdf?5f7229e446c85
5 | R1,R2 | 2 | Generic | Generic | 18kΩ 1/16W 2% | 0402 | SMD | Generic
6 | R3,R4,R5 | 3 | Generic | Generic | 2.2kΩ 1/16W 2% | 0402 | SMD | Generic
7 | U1 | 1 | AMS | AS5048B | AS5048B | TSSOP-14 | SMD | https://ams.com/documents/20143/36005/AS5048_DS000298_4-00.pdf

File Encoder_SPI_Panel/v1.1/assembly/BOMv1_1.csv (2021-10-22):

Item | Ref Des | Qty | Manufacturer | Mfg Part # | Description / Value | Package | Type | Your Instructions / Notes
1 | B6-U1 | 1 | AMS | AS5048A-HTSP | AS5048A | TSSOP-14_4.4x5mm_P0.65mm | SMD
2 | B5-R1,B5-R2 | 2 | Generic | Generic | 18k | R_0402_1005Metric | SMD | Generic Resistor, 0402
3 | B5-R3,B5-R4 | 2 | Generic | Generic | 2k2 | R_0402_1005Metric | SMD | Generic Resistor, 0402
4 | B5-J1 | 1 | JST | SH_SM04B-SRSS-TB_1x04-1MP_P1.00mm_Horizontal | Conn_01x04 | JST_SH_SM04B-SRSS-TB_1x04-1MP_P1.00mm_Horizontal | SMD
5 | B5-U1 | 1 | AMS | AS5048B-HTSP | AS5048B | TSSOP-14_4.4x5mm_P0.65mm | SMD
6 | B4-C2,B3-C2 | 2 | Murata | GRM155C80J105KA12D | 1uF 6.3V | C_0402_1005Metric | SMD | or similar 6.3V 1uF capacitor; Unpolarized capacitor;
7 | B4-D1,B3-D1,B2-D1,B1-D1,B6-D1,B5-D1 | 6 | Wurth | 150040VS73240 | green | LED_0402_1005Metric | SMD
8 | B4-R1,B3-R1,B2-R1,B1-R1,B6-R5,B5-R5 | 6 | Generic | Generic | 1k | R_0402_1005Metric | SMD | Generic Resistor, 0402
9 | B4-U1,B3-U1 | 2 | Monolithic Power Systems (MPS) | MA730GQ | MA730 | QFN-16-1EP_3x3mm_P0.5mm_EP1.75x1.75mm | SMD
10 | B4-J1,B3-J1 | 2 | JST | SH_SM08B-SRSS-TB_1x08-1MP_P1.00mm_Horizontal | Conn_01x08_MountingPin | JST_SH_SM08B-SRSS-TB_1x08-1MP_P1.00mm_Horizontal | SMD
11 | B2-J1,B1-J1,B6-J1 | 3 | JST | SH_SM06B-SRSS-TB_1x06-1MP_P1.00mm_Horizontal | Conn_01x06_MountingPin | JST_SH_SM06B-SRSS-TB_1x06-1MP_P1.00mm_Horizontal | SMD
12 | B2-C2,B1-C1,B6-C2,B5-C2 | 4 | AVX | 04026D104KAT2A | 100nF 6.3V | C_0402_1005Metric | SMD | or similar 6.3V 100nF capacitor; Unpolarized capacitor;
13 | B2-U1 | 1 | Infineon | TLE5012BE1000XUMA1 | TLE5012B | Infineon_PG-DSO-8 | SMD
14 | B1-C2,B6-C1,B5-C1 | 3 | Murata | GRM155R60J106ME15D | 10uF 6.3V | C_0402_1005Metric | SMD | or other 6.3V 10uF capacitor; Unpolarized capacitor;
15 | B1-U1 | 1 | Broadcom | AEAT-8800-Q24TR | AEAT_8800_Q24 | QFN-24-1EP_5x5mm_P0.65mm_EP3.2x3.2mm | SMD

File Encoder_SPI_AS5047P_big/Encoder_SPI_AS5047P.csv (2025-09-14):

Item | Ref Des | Qty | Manufacturer | Mfg Part # | Description / Value | Package | Type | Your Instructions / Notes
1 | C1 | 1 | Generic | 1uF 10V | 1uF 10V | C_0603_1608Metric | ? | eg. YAGEO CC0603KRX7R6BB105; Unpolarized capacitor;
2 | C2 | 1 | Generic | 100nF 10V | 100nF 10V | C_0603_1608Metric | ? | eg. YAGEO CC0603KRX7R6BB104; Unpolarized capacitor;
3 | D1 | 1 | Generic | Green LED | green | LED_0805_2012Metric | ? | e.g. XINGLIGHT XL-2012UGC; Light emitting diode;
4 | J1,J2 | 2 | Scondar Electronic Limited | SCT-WR-S-06P | Conn_01x06_MountingPin | JST_SH_SM06B-SRSS-TB_1x06-1MP_P1.00mm_Horizontal | ? | compatible to JST SH_SM06B-SRSS-TB_1x06-1MP_P1.00mm_Horizontal; Generic connectable mounting pin connector, single row, 01x06, script generated (kicad-library-utils/schlib/autogen/connector/);
5 | R1 | 1 | Generic | Generic 2k2 Resistor | 2k2 | R_0603_1608Metric | ? | ; Resistor;
6 | U2 | 1 | AMS | AS5047U-HTSM or | AS5047D | TSSOP-14_4.4x5mm_P0.65mm | ? | Depends on price also: AS5047P-ATSM; On-Axis Magnetic Position Sensor, 14-bit, PWM Output, ABI Output, UVW Output, SPI Interface, TSSOP-14; https://ams.com/documents/20143/36005/AS5047D_DS000394_2-00.pdf

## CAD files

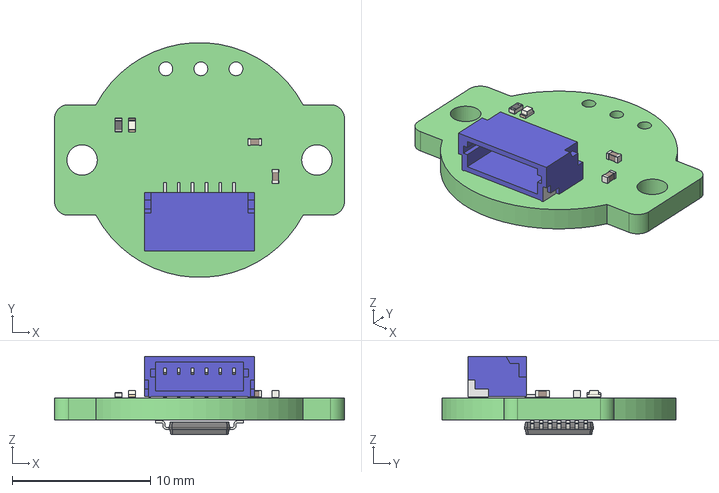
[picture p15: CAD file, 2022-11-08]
Encoder_SPI/Encoder.step
21.0 x 17.0 x 5.66 mm
Encoder PCB

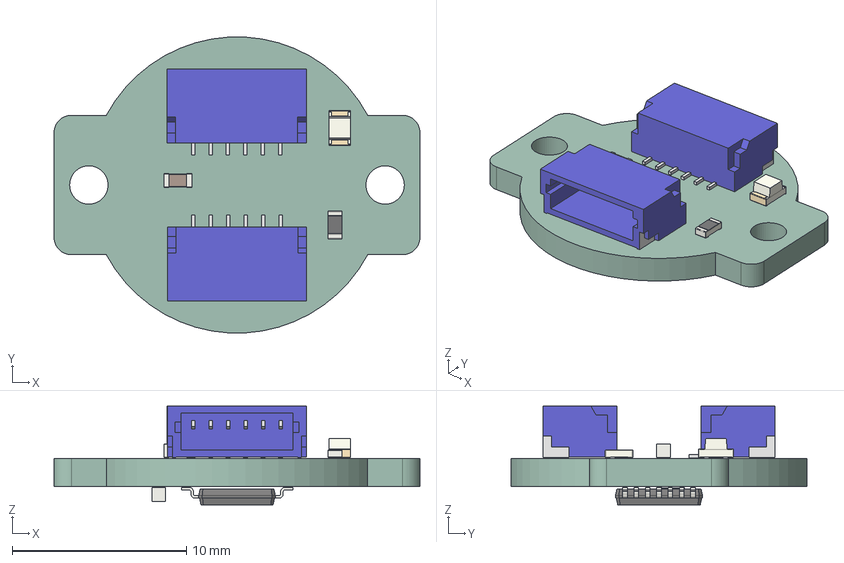
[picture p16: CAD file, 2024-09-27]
Encoder_SPI_AS5047P_big/Encoder_SPI_AS5047P.step
21.0 x 17.0 x 5.66 mm
SM06B-SRSS x 2
R_0603_1608Metric
LED_0805_2012Metric
C_0603_1608Metric x 2
TSSOP_14_44x5mm_P065mm
Encoder_SPI_AS5047P_PCB

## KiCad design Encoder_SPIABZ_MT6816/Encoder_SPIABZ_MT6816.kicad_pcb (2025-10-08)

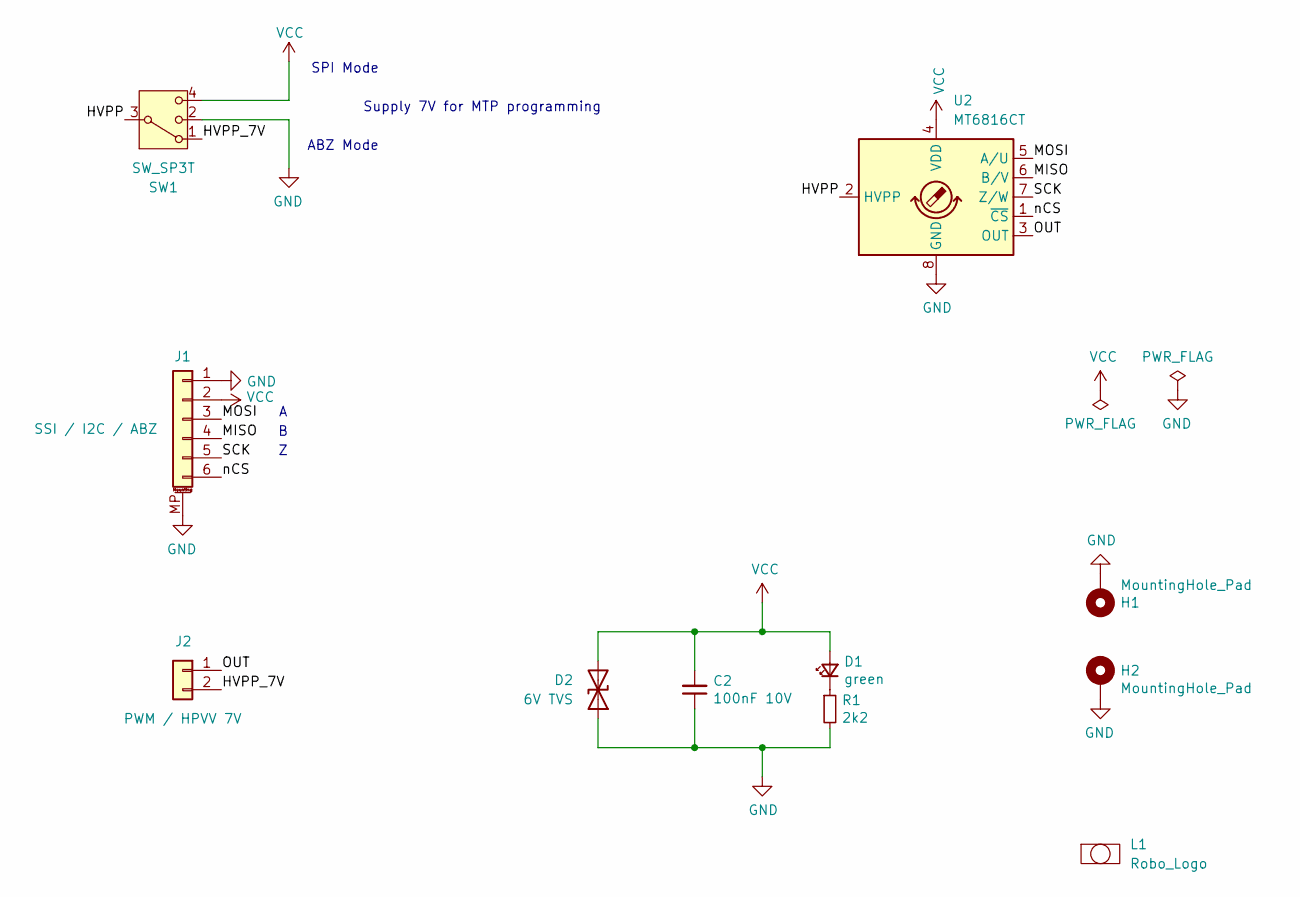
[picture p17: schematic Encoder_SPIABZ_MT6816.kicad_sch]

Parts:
C2: 100nF 10V; C_0603_1608Metric; Part GRM155R71A104KA01J
D1: green; LED_0603_1608Metric; Part 150040VS73240
D2: 6V TVS; D_0603_1608Metric; Part SP1005-01WTG
H1, H2: MountingHole_Pad; MountingHole_2.2mm_M2_ISO7380_Pad
J1: Conn_01x06_MountingPin; JST_SH_SM06B-SRSS-TB_1x06-1MP_P1.00mm_Horizontal; Part SCT-WR-S-06P
J2: Conn_01x02; PinHeader_1x02_P2.54mm_Vertical
L1: Robo_Logo; Robo_logo2
R1: 2k2; R_0603_1608Metric; Part Generic 2k2 Resistor
SW1: SW_SP3T; SLM-13-755-T50; Part SLM-13-755-T50; JLC C370968
U2: MT6816CT; SO-8_3.9x4.9mm_P1.27mm

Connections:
/HVPP: SW1.3, U2.2 (HVPP)
/HVPP_7V: J2.2, SW1.1
/MISO: J1.4, U2.6 (B/V)
/MOSI: J1.3, U2.5 (A/U)
/OUT: J2.1, U2.3 (OUT)
/SCK: J1.5, U2.7 (Z/W)
/nCS: J1.6, U2.1 (~CS)
GND: C2.1, D2.1 (A1), H1.1, H2.1, J1.1, J1.MP (MountPin), R1.2, SW1.2, SW1.MP, U2.8 (GND)
unnamed: D1.1 (K), R1.1
VCC: C2.2, D1.2 (A), D2.2 (A2), J1.2, SW1.4, U2.4 (VDD)

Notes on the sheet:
ABZ Mode
Supply 7V for MTP programming
SPI Mode

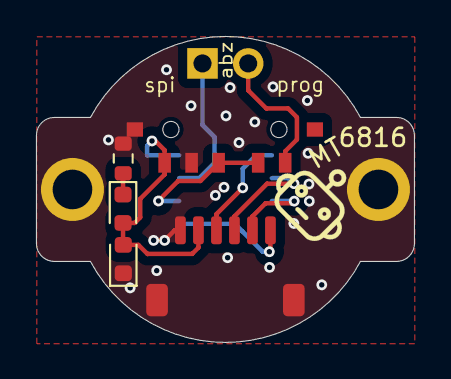
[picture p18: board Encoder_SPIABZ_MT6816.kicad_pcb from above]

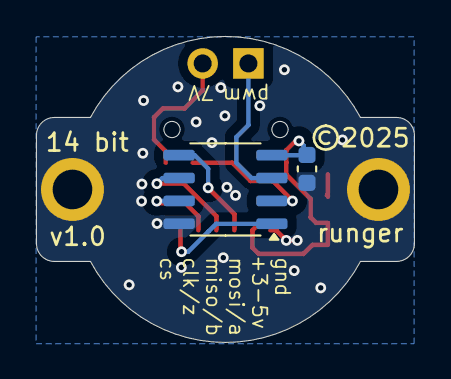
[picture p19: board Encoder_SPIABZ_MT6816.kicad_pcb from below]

Board: 2 copper layers, 21.0 x 17.0 mm, 11 parts (2 on the bottom side), 10 nets.

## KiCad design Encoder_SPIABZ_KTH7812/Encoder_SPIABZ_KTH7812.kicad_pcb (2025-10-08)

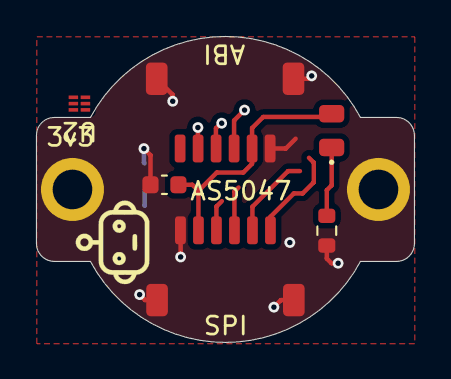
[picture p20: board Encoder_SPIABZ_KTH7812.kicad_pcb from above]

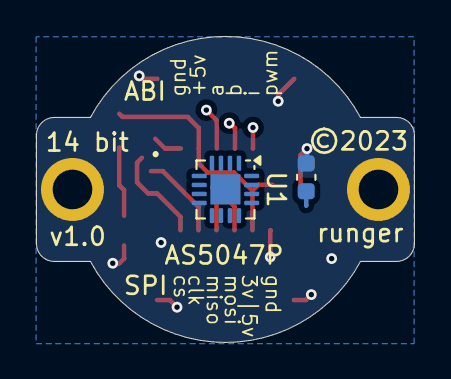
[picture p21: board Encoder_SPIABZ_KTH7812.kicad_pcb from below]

Board: 2 copper layers, 21.0 x 17.0 mm, 13 parts (2 on the bottom side), 13 nets.

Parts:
C1: 10uF 10V; C_0603_1608Metric
C2: 100nF 10V; C_0603_1608Metric
D1: green; LED_0805_2012Metric
H1, H2: MountingHole_Pad; MountingHole_2.2mm_M2_ISO7380_Pad
J1, J2: Conn_01x06_MountingPin; JST_SH_SM06B-SRSS-TB_1x06-1MP_P1.00mm_Horizontal
L1: Robo_Logo; Robo_logo2
R1: 2k2; R_0603_1608Metric
T1, T2: Tab
U1: KTH7812-X-X-QFN16-L; QFN-16-1EP_3x3mm_P0.5mm_EP1.675x1.675mm
U2: 74LVC1G97; DSF6

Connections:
/A: J2.3, U1.2 (A)
/B: J2.4, U1.6 (B)
/I: J2.5, U1.3 (Z)
/MGHL: J2.6, U2.4 (Y)
/MISO: J1.4, U1.7 (MISO)
/MOSI: J1.3, U1.4 (MOSI)
/SCK: J1.5, U1.12 (SCLK)
/nCS: J1.6, U1.5 (CS)
GND: C1.1, C2.1, H1.1, H2.1, J1.1, J1.MP (MountPin), J2.1, J2.MP (MountPin), R1.2, U1.8 (GND), U1.10 (TEST), U2.2 (GND), U2.3 (IN0)
unnamed: D1.1 (K), R1.1
unnamed: U1.16 (MGH), U2.1 (IN1)
unnamed: U1.11 (MGL), U2.6 (IN2)
VCC: C1.2, C2.2, D1.2 (A), J1.2, J2.2, U1.13 (VDD), U2.5 (VCC)

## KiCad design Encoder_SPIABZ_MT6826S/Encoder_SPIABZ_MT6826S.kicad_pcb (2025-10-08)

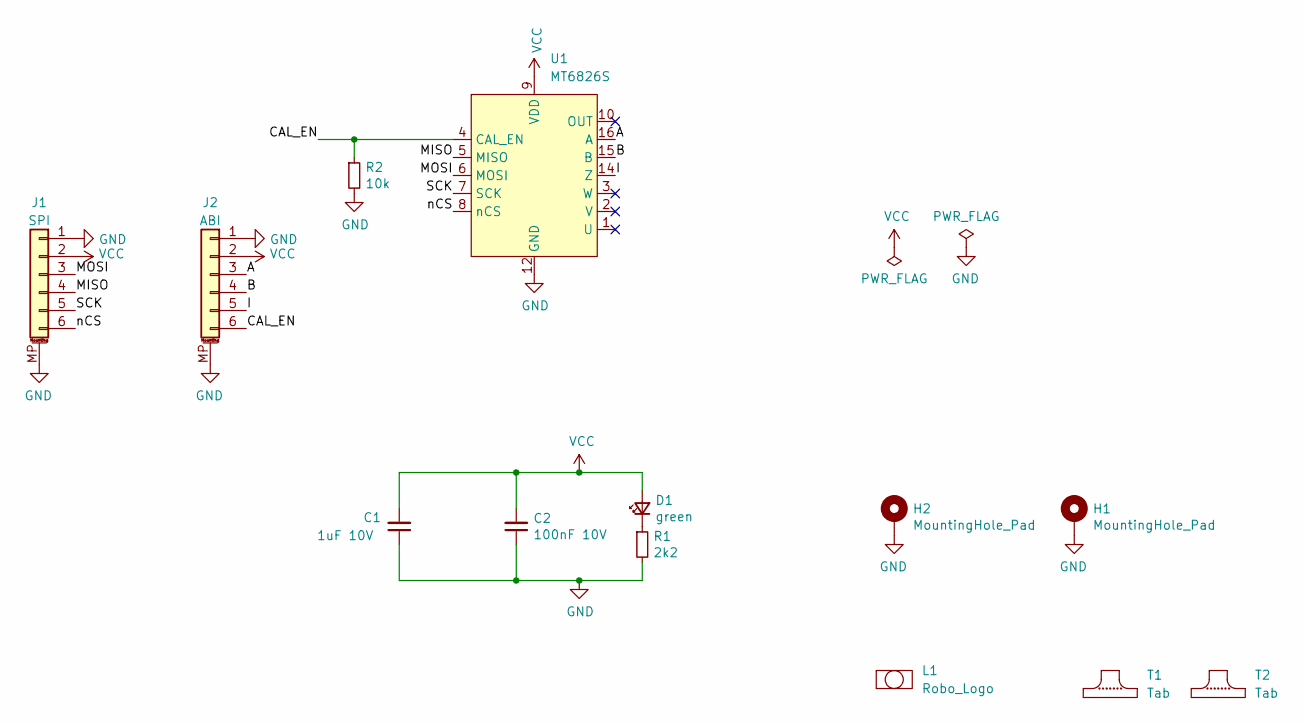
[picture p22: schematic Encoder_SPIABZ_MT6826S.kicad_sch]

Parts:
C1: 1uF 10V; C_0603_1608Metric; Part 1uF 10V
C2: 100nF 10V; C_0603_1608Metric; Part 100nF 10V
D1: green; LED_0805_2012Metric; Part Green LED
H1, H2: MountingHole_Pad; MountingHole_2.2mm_M2_ISO7380_Pad
J1, J2: Conn_01x06_MountingPin; JST_SH_SM06B-SRSS-TB_1x06-1MP_P1.00mm_Horizontal; Part SCT-WR-S-06P
L1: Robo_Logo; Robo_logo2
R1: 2k2; R_0603_1608Metric; Part Generic 2k2 Resistor
R2: 10k; R_0603_1608Metric; Part 10k
T1, T2: Tab
U1: MT6826S; TSSOP-16_4.4x5mm_P0.65mm; Part MT6835GT-STD

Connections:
/A: J2.3, U1.16 (A)
/B: J2.4, U1.15 (B)
/CAL_EN: J2.6, R2.1, U1.4 (CAL_EN)
/I: J2.5, U1.14 (Z)
/MISO: J1.4, U1.5 (MISO)
/MOSI: J1.3, U1.6 (MOSI)
/SCK: J1.5, U1.7 (SCK)
/nCS: J1.6, U1.8 (nCS)
GND: C1.1, C2.1, H1.1, H2.1, J1.1, J1.MP (MountPin), J2.1, J2.MP (MountPin), R1.2, R2.2, U1.12 (GND)
unnamed: D1.1 (K), R1.1
VCC: C1.2, C2.2, D1.2 (A), J1.2, J2.2, U1.9 (VDD)

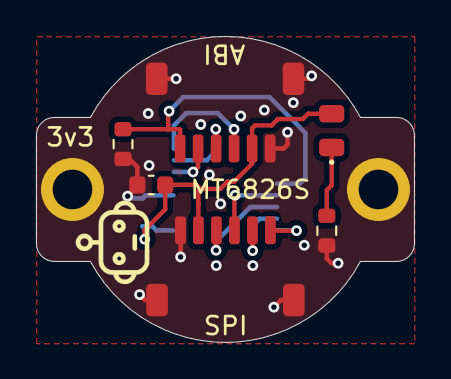
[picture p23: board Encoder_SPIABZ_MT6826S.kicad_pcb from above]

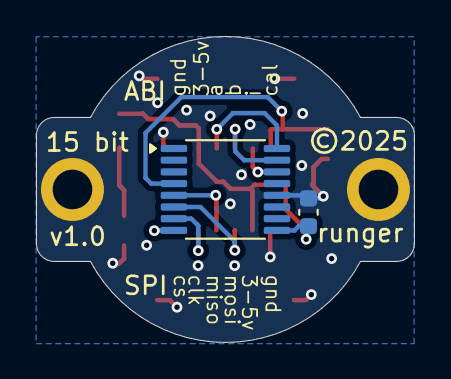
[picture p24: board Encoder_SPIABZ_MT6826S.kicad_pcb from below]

Board: 2 copper layers, 21.0 x 17.0 mm, 13 parts (2 on the bottom side), 11 nets.

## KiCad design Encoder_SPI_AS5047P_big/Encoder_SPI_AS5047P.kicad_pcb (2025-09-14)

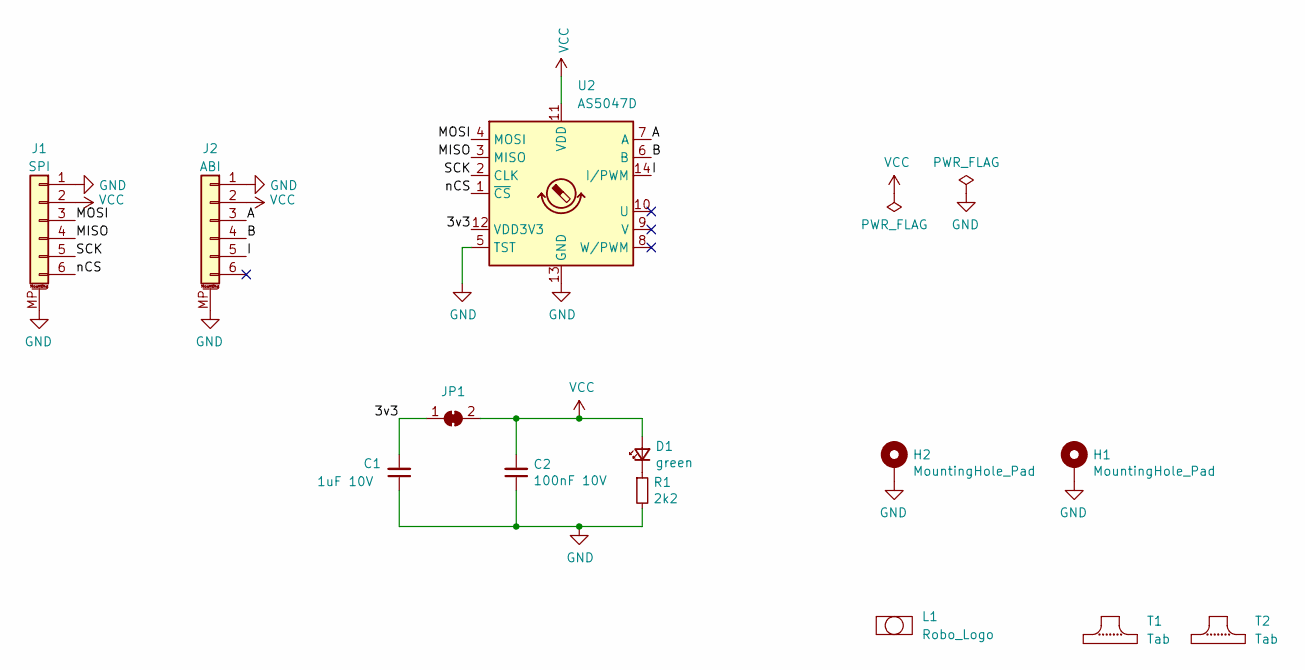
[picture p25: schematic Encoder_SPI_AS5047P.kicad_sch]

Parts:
C1: 1uF 10V; C_0603_1608Metric; Part 1uF 10V
C2: 100nF 10V; C_0603_1608Metric; Part 100nF 10V
D1: green; LED_0805_2012Metric; Part Green LED
H1, H2: MountingHole_Pad; MountingHole_2.2mm_M2_ISO7380_Pad
J1, J2: Conn_01x06_MountingPin; JST_SH_SM06B-SRSS-TB_1x06-1MP_P1.00mm_Horizontal; Part SCT-WR-S-06P
JP1: SolderJumper_2_Bridged; SolderJumper-2_P1.3mm_Bridged_RoundedPad1.0x1.5mm
L1: Robo_Logo; Robo_logo2
R1: 2k2; R_0603_1608Metric; Part Generic 2k2 Resistor
T1, T2: Tab
U2: AS5047D; TSSOP-14_4.4x5mm_P0.65mm; Part AS5047U-HTSM or

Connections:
/3v3: C1.2, JP1.1 (A), U2.12 (VDD3V3)
/A: J2.3, U2.7 (A)
/B: J2.4, U2.6 (B)
/I: J2.5, U2.14 (I/PWM)
/MISO: J1.4, U2.3 (MISO)
/MOSI: J1.3, U2.4 (MOSI)
/SCK: J1.5, U2.2 (CLK)
/nCS: J1.6, U2.1 (~CS)
GND: C1.1, C2.1, H1.1, H2.1, J1.1, J1.MP (MountPin), J2.1, J2.MP (MountPin), R1.2, U2.5 (TST), U2.13 (GND)
unnamed: D1.1 (K), R1.1
VCC: C2.2, D1.2 (A), J1.2, J2.2, JP1.2 (B), U2.11 (VDD)

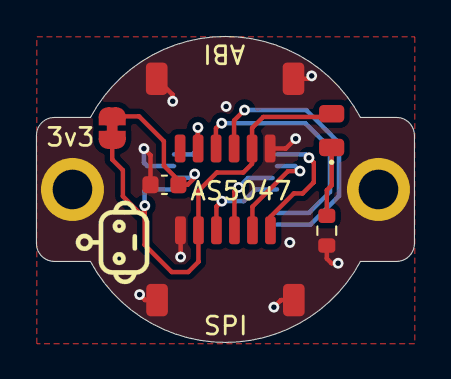
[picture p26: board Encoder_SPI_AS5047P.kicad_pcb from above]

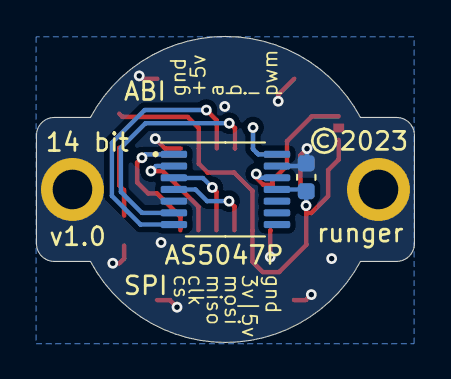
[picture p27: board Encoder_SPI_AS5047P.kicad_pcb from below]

Board: 2 copper layers, 21.0 x 17.0 mm, 13 parts (2 on the bottom side), 11 nets.

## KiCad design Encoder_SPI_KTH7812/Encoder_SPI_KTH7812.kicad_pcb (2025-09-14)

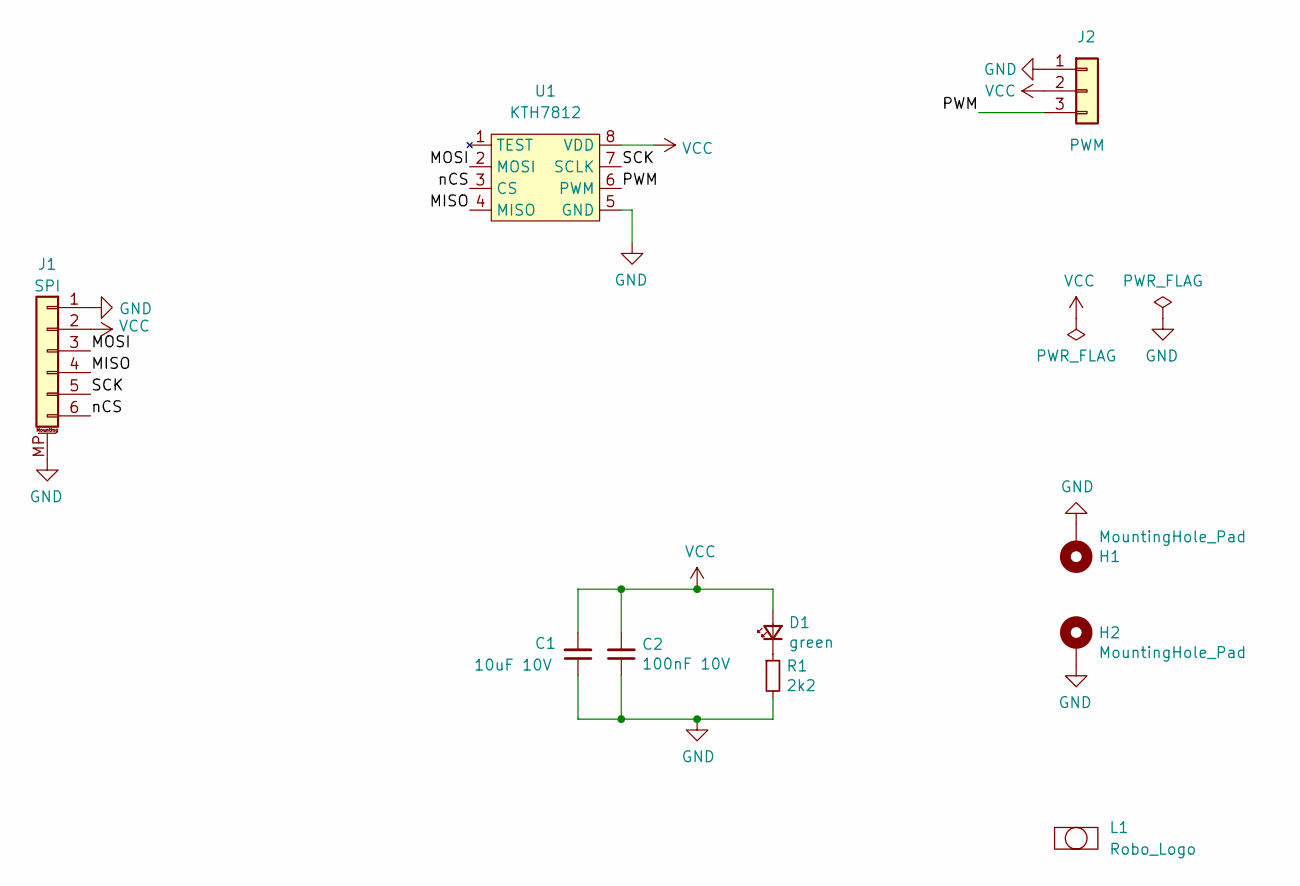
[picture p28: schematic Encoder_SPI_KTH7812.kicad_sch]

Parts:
C1: 10uF 10V; C_0805_2012Metric
C2: 100nF 10V; C_0603_1608Metric
D1: green; LED_0805_2012Metric
H1, H2: MountingHole_Pad; MountingHole_2.2mm_M2_ISO7380_Pad
J1: Conn_01x06_MountingPin; JST_SH_SM06B-SRSS-TB_1x06-1MP_P1.00mm_Horizontal; Part SCT-WR-S-06P
J2: Conn_01x03; PinHeader_1x03_P2.54mm_Vertical
L1: Robo_Logo; Robo_logo2
R1: 2k2; R_0805_2012Metric; Part Generic 2k2 Resistor
U1: KTH7812; SOP-8_3.76x4.96mm_P1.27mm

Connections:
/MISO: J1.4, U1.4 (MISO)
/MOSI: J1.3, U1.2 (MOSI)
/PWM: J2.3, U1.6 (PWM)
/SCK: J1.5, U1.7 (SCLK)
/nCS: J1.6, U1.3 (CS)
GND: C1.1, C2.1, H1.1, H2.1, J1.1, J1.MP (MountPin), J2.1, R1.2, U1.5 (GND)
unnamed: D1.1 (K), R1.1
VCC: C1.2, C2.2, D1.2 (A), J1.2, J2.2, U1.8 (VDD)



Board: 2 copper layers, 21.0 x 17.0 mm, 10 parts (2 on the bottom side), 8 nets.

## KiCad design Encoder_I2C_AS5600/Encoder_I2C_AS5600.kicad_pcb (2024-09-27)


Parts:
C1: 10uF; C_0603_1608Metric
C2: 100nF; C_0603_1608Metric
D1: LED green; LED_0603_1608Metric
H1, H2: MountingHole_Pad; MountingHole_2.2mm_M2_ISO7380_Pad
IC1: AS5600L; SOIC-8_3.9x4.9mm_P1.27mm; Part AS5600L-ASOM
J1: Conn_01x04; JST_SH_SM04B-SRSS-TB_1x04-1MP_P1.00mm_Horizontal; Part SH_SM04B-SRSS-TB_1x04-1MP
J3: Conn_01x03; PinHeader_1x03_P2.54mm_Vertical
R1: 2k2; R_0603_1608Metric
R2, R3: 5k1; R_0603_1608Metric

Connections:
/OUT: IC1.3 (OUT), J3.2
/SCL: IC1.7 (SCL), J1.4, R3.2
/SDA: IC1.6 (SDA), J1.3, R2.2
GND: C1.2, C2.1, D1.1 (K), H1.1, H2.1, IC1.4 (GND), IC1.8 (DIR), J3.1
unnamed: D1.2 (A), R1.2
VDD: C1.1, C2.2, IC1.1 (VDD5V), IC1.2 (VDD3V3), J1.2, J3.3, R1.1, R2.1, R3.1



Board: 2 copper layers, 21.0 x 17.0 mm, 13 parts (2 on the bottom side), 6 nets.

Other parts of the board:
T1, T2: Tab

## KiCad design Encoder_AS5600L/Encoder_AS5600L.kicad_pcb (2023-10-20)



Board: 2 copper layers, 21.0 x 10.0 mm, 12 parts (3 on the bottom side), 7 nets, no tracks yet.

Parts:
C1: 1uF 10V; C_0603_1608Metric
C2: 100nF 10V; C_0603_1608Metric
D1: green; LED_0805_2012Metric
H1, H2: MountingHole_Pad; MountingHole_2.2mm_M2_ISO7380_Pad
J1: JST_SH_SM04B; JST_SH_SM04B-SRSS-TB_1x04-1MP_P1.00mm_Horizontal
JP1: SolderJumper_2_Bridged; SolderJumper-2_P1.3mm_Bridged_RoundedPad1.0x1.5mm
L1: Robo_Logo; Robo_logo2
R1, R2, R3: 2k2; R_0603_1608Metric
U2: AS5600L; AS5600

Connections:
/3v3: C1.2, JP1.1 (A), U2.C3 (VDD3V3)
/SCL_A: J1.4, R1.2, U2.B1 (SCL)
/SDA_A: J1.3, R2.2, U2.D1 (SDA)
GND: C1.1, C2.1, H1.1, H2.1, J1.1, J1.MP (MountPin), R3.2, U2.A1 (DIR), U2.A2 (TEST), U2.C1 (TEST), U2.E2 (TEST), U2.E3 (GND)
unnamed: D1.1 (K), R3.1
VCC: C2.2, D1.2 (A), JP1.2 (B), U2.A3 (VDD5V), U2.E1 (PGO)
VDD: J1.2, R1.1, R2.1

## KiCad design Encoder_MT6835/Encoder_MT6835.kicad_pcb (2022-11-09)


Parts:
C1: 100nF 10V; C_0402_1005Metric; Part GRM155R71A104KA01J
D1: 6V TVS; D_0201_0603Metric; Part SP1005-01WTG
D2: green; LED_0402_1005Metric; Part 150040VS73240
H1, H2: MountingHole_Pad; MountingHole_2.2mm_M2_ISO7380_Pad
J1, J3: Conn_01x06_MountingPin; JST_SH_SM06B-SRSS-TB_1x06-1MP_P1.00mm_Horizontal; Part Connector_JST:JST_SH_SM06B-SRSS-TB_1x06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
J2: Pad_OUT; PinHeader_1x01_P2.54mm_Vertical
L1: Robo_Logo; Robo_logo2
R1: 2k2; R_0402_1005Metric; Part Generic 2k2 Resistor
U1: MT6835; TSSOP-16_4.4x5mm_P0.65mm; Part MT6835GT-STD

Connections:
/ABI_A: J3.3, U1.16 (A)
/ABI_B: J3.4, U1.15 (B)
/ABI_I: J3.5, U1.14 (Z)
/CAL_EN: J3.6, U1.4 (CAL_EN)
/MISO: J1.4, U1.5 (MISO)
/MOSI: J1.3, U1.6 (MOSI)
/PWM: J2.1, U1.10 (OUT)
/SCK: J1.5, U1.7 (SCK)
/nCS: J1.6, U1.8 (nCS)
GND: C1.1, D1.1 (A1), H2.1, J1.1, J1.MP (MountPin), J3.1, J3.MP (MountPin), R1.2, U1.12 (GND)
unnamed: D2.1 (K), R1.1
VCC: C1.2, D1.2 (A2), D2.2 (A), H1.1, J1.2, J3.2, U1.9 (VDD)

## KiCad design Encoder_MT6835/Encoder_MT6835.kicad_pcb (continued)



Board: 2 copper layers, 21.0 x 17.0 mm, 11 parts (2 on the bottom side), 12 nets.

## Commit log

2021-10-22 first import of all the encoder projects
    [BOM.csv, BOM_LikePreviousOrder.xls, BOMv1_1.csv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]
2022-01-18 Encoder_SPI update for new assembly order
    [BOM.csv, Encoder.kicad_pcb, Encoder.kicad_sch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]
2022-01-18 added readme and documentation images
    [Encoder.kicad_sch]
2022-01-23 add PCB images and update README
2022-01-27 A1334 encoder design first production run
    [Encoder_SPI_A1333.kicad_pcb, Encoder_SPI_A1333.kicad_sch, Encoder_SPI_A1334.kicad_pcb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]
2022-01-27 updated docs for AS5048A sensor
2022-02-08 Added design based on SC60228 encoder
    [Encoder_SPI_SC60228.kicad_pcb, Encoder_SPI_SC60228.kicad_sch]
2022-05-04 new encoder models, updated READMEs
    [Encoder_SPI_MA330.csv, Encoder_SPI_MA330.kicad_pcb, Encoder_SPI_MA330.kicad_sch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]
2022-11-05 Created a MT6835 encoder board with SPI and ABZ
    [Encoder_MT6835.kicad_pcb, Encoder_MT6835.kicad_sch]
2022-11-08 fix incorrect footprint
    [Encoder_SPI_MT6701_I2CAdapter.kicad_pcb, Encoder_SPI_MT6701_I2CAdapter.kicad_sch]
2022-11-08 update labels
    [Encoder_SPI_MA330.kicad_sch, Encoder_SPI_MT6701.kicad_sch]
2022-11-08 add 3d models, fix bugs
    [Encoder.kicad_pcb, Encoder.step, Encoder_SPI_MT6701_I2CAdapter.kicad_sch]
2022-11-09 production v1
    [Encoder_MT6835.csv, Encoder_MT6835.kicad_pcb, Encoder_MT6835.kicad_sch]
2023-05-14 Encoder updates
    [Encoder_SPI_SC60228.kicad_pcb, Encoder_SPI_SC60228.kicad_sch, Encoder_SPI_SC60228_panel.kicad_pcb]
2023-09-22 Add AS5047P encoder board
    [Encoder_SPI_AS5047P.kicad_pcb, Encoder_SPI_AS5047P.kicad_sch]
2023-10-20 added AS5600 encoder (unfinished)
    [Encoder_AS5600L.kicad_pcb, Encoder_AS5600L.kicad_sch]
2024-01-18 Working on docs for AS5047P
    [Encoder_SPI_AS5047P.step]
2024-09-27 AS5600 I2C encoder board and panel
    [Encoder_I2C_AS5600.kicad_pcb, Encoder_I2C_AS5600.kicad_sch]
2024-09-27 AS5047P encoder changes
    [Encoder_SPI_AS5047P.kicad_pcb, Encoder_SPI_AS5047P.step]
2025-10-08 new encoders - KTH7812, MT6816, MT6826S
    [Encoder_SPIABZ_KTH7812.kicad_pcb, Encoder_SPIABZ_MT6816.kicad_pcb, Encoder_SPIABZ_MT6816.kicad_sch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]
2026-01-04 encoder small changes

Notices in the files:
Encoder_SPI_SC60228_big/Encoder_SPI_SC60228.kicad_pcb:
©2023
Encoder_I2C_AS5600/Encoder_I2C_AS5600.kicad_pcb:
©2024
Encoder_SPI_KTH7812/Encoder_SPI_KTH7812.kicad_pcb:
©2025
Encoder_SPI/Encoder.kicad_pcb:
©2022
